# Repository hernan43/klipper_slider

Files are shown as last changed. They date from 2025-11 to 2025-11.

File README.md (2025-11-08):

# DIY Slider Build
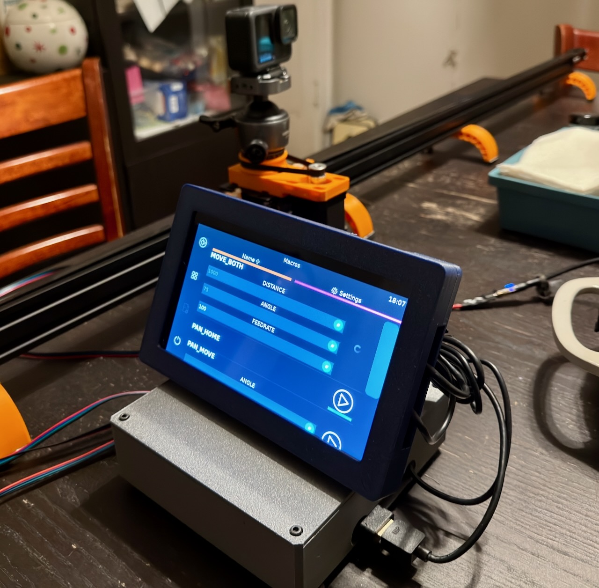
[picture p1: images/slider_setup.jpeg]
Shot of fully built camera slider with pan head and control box/touchscreen


## Hardware
 * [Raspberry Pi 4 Model B 4GB](https://www.pishop.us/product/raspberry-pi-4-model-b-4gb/)
 * [SKR Pico](https://www.amazon.com/BIGTREETECH-Controller-Raspberry-Printing-Motherboard/dp/B09MYKL9MP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)
 * [V slot 2040 aluminum extrusion](https://www.amazon.com/Aluminum-Extrusion-European-Standard-Anodized/dp/B0CLH61BRK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) - whatever length you want
 * [Nema 17 stepper motors](https://www.amazon.com/STEPPERONLINE-Stepper-Bipolar-Printer-Extruder/dp/B0B93J9QZY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)
 * [V slot gantry plate](https://www.amazon.com/SeekLiny-Gantry-Wheels-Aluminum-Extrusion/dp/B0CX7TQQVK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)
 * [6mm idler pulley](https://www.amazon.com/uxcell-Aluminum-Timing-Synchronous-Printer/dp/B0DK3M68YW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)
 * [6mm GT2 timing belt](https://www.amazon.com/Upgrade-Non-Slip-Version-Printer-Printers/dp/B08R93QQ8Z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) - enough for the length of aluminum extrusion you chose
 * [Nema 17 mounting plate](https://www.amazon.com/STEPPERONLINE-Mounting-Bracket-Stepper-Economy/dp/B09LCSBLF8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)
 * [Creality style GT2 belt tensioner](https://www.amazon.com/AEDIKO-Upgraded-Tensioner-Straighten-Creality/dp/B09GF7CN37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)
 * [M4 screws and t-nuts](https://www.amazon.com/Camming-Replacement-Compatible-Standard-Systems/dp/B0B83TGWVT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) - You might need a variety of sizes depending on your part choices

### Pan specific parts
 
 * [35mm thrust bearing](https://www.amazon.com/AXK2035-Thrust-Needle-Bearings-Washers/dp/B0F4X2QCFP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)
 * [8mm thrust bearing](https://www.amazon.com/uxcell-F8-16M-Miniature-Bearings-8x16x5mm/dp/B07QLTXJDH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)
 * [228-2GT-6 Pulley Belt](https://www.amazon.com/dp/B0CMHYBKVN?ref=ppx_yo2ov_dt_b_fed_asin_title&th=1)
 * [3D printed rotating base](https://www.printables.com/model/232492-diy-camera-slider/files)
 * [3D printed mounting plate for tripod head](https://www.printables.com/model/1473628-modified-pan-head-platform)

## Software
 
 * [MainsailOS](https://docs-os.mainsail.xyz/)

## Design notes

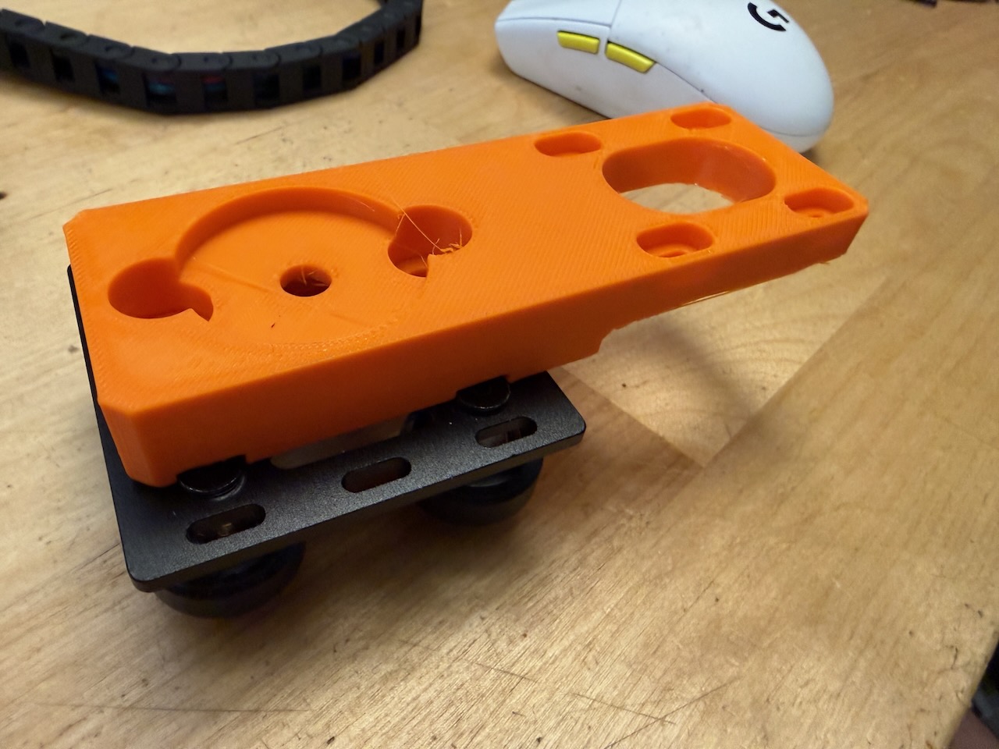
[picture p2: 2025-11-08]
images/slider pan mount.jpeg

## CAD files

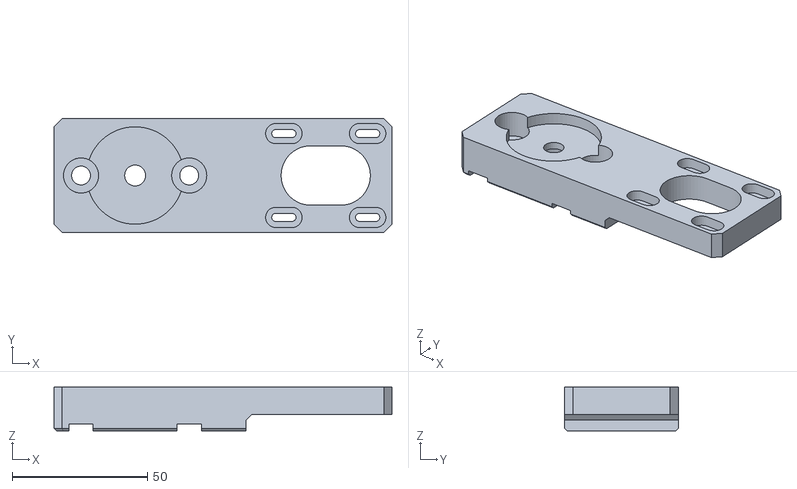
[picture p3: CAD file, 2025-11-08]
STLs/Pan Head mount v14.stl
125.0 x 42.0 x 16.2

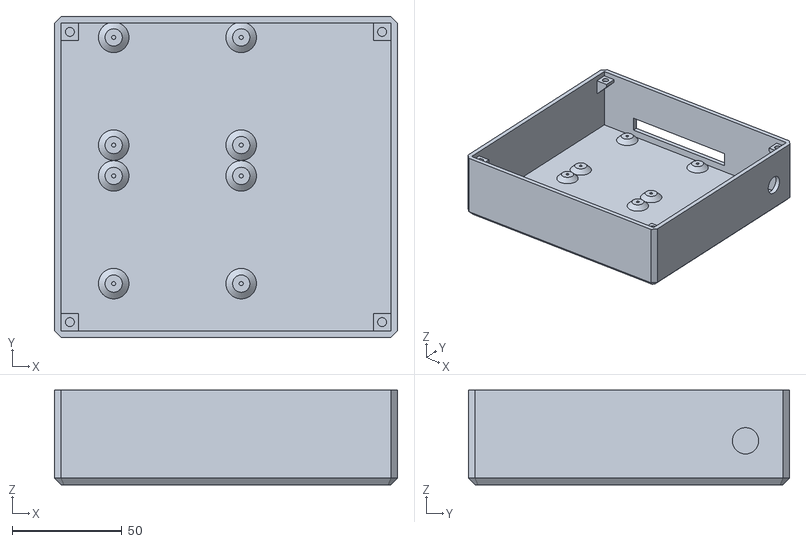
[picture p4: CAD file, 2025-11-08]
STLs/SKR Pico Shell Lower.stl
156.0 x 146.0 x 43.0

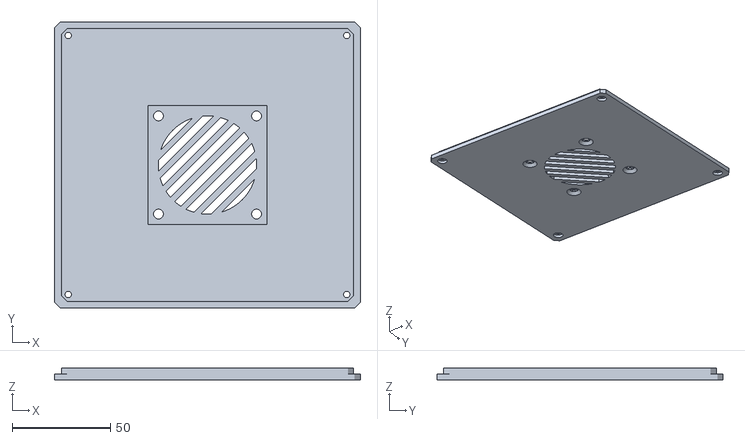
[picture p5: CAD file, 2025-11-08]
STLs/SKR Pico Shell Lid.stl
156.0 x 146.0 x 6.00

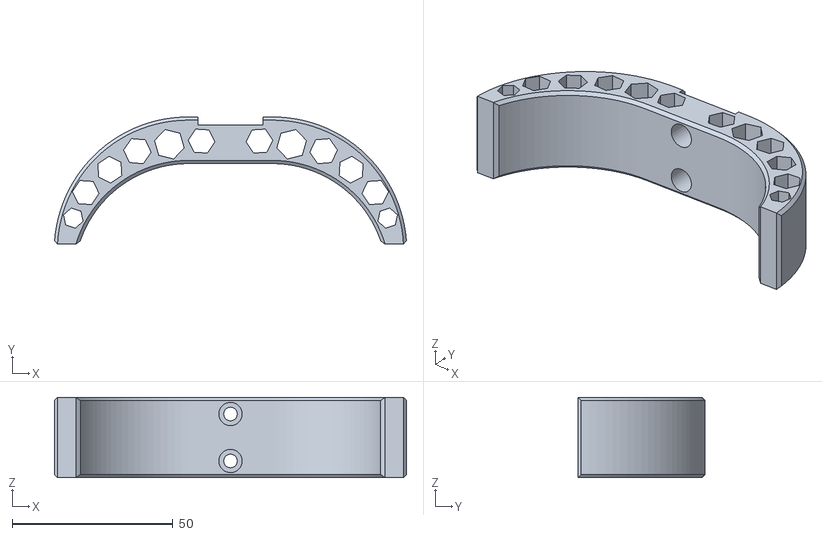
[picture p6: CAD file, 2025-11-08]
STLs/Extrusion foot v10.stl
109.4 x 39.5 x 25.0

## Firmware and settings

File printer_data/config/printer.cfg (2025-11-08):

[include mainsail.cfg]

[mcu]
#serial: /dev/serial/by-id/usb-Klipper_rp2040_504450612065BD1C-if00
serial: /dev/ttyAMA0

# ========= Printer =========
[printer]
kinematics: cartesian
max_velocity: 600
max_accel: 2000
square_corner_velocity: 5.0
# Trick Klipper: disable Z movement (0 height)
max_z_velocity: 1
max_z_accel: 1

# ========= X Axis (Slider) =========
[stepper_x]
step_pin: gpio11
dir_pin: !gpio10
enable_pin: !gpio12
microsteps: 16
rotation_distance: 40.0      # adjust for belt or leadscrew
endstop_pin: tmc2209_stepper_x:virtual_endstop
position_min: 0
position_endstop: 0
position_max: 1100             # slider length in mm
homing_speed: 40
homing_retract_dist: 0
homing_positive_dir: false

[tmc2209 stepper_x]
uart_pin: gpio9
tx_pin: gpio8
uart_address: 0
diag_pin: ^gpio4
run_current: 0.60
stealthchop_threshold: 0
driver_SGTHRS: 50             # higher = more sensitive (try 40–80 range)

# ========= Y Axis (Pan) =========
[stepper_y]
step_pin: gpio6
dir_pin: !gpio5
enable_pin: !gpio7
microsteps: 16
rotation_distance: 40.0     # degrees per motor rev, adjust for gearing
endstop_pin: tmc2209_stepper_y:virtual_endstop
position_endstop: 0
position_min: -180
position_max: 180             # pan range
homing_speed: 20
homing_retract_dist: 0
homing_positive_dir: false

[tmc2209 stepper_y]
uart_pin: gpio9
tx_pin: gpio8
uart_address: 2
diag_pin: ^gpio3
run_current: 0.70
stealthchop_threshold: 0
driver_SGTHRS: 50

# ========= Dummy Z (required placeholder) =========
# This prevents Klipper from complaining that no Z axis exists
[stepper_z]
step_pin: gpio19
dir_pin: gpio28
enable_pin: !gpio2
microsteps: 16
rotation_distance: 8
endstop_pin: ^gpio25
position_endstop: 0.0
position_max: 250

# ========= Macros =========
[idle_timeout]
timeout: 60       # seconds before idle triggers
gcode:
  SET_TMC_CURRENT STEPPER=stepper_x HOLD_CURRENT=0.10
  SET_TMC_CURRENT STEPPER=stepper_y HOLD_CURRENT=0.10

# ========= Sensorless Homing Mode Toggle =========
[gcode_macro SENSORLESS_HOMING_ON]
description: "Enable SpreadCycle for reliable sensorless homing"
gcode:
  M118 Enabling SpreadCycle mode for homing...
  # X axis
  SET_TMC_FIELD STEPPER=stepper_x FIELD=TPWMTHRS VALUE=0
  # Y axis
  SET_TMC_FIELD STEPPER=stepper_y FIELD=TPWMTHRS VALUE=0

[gcode_macro SENSORLESS_HOMING_OFF]
description: "Re-enable quiet StealthChop mode after homing"
gcode:
  M118 Enabling StealthChop for quiet operation...
  # X axis
  SET_TMC_FIELD STEPPER=stepper_x FIELD=TPWMTHRS VALUE=999999
  # Y axis
  SET_TMC_FIELD STEPPER=stepper_y FIELD=TPWMTHRS VALUE=999999

[gcode_macro MOVE_BOTH]
description: "Move slider (X) and pan (Y) together with angle calculation"
gcode:
  {% set x = params.DISTANCE|default(1000)|float %}
  {% set angle = params.ANGLE|default(75)|float %}
  {% set feed = params.FEEDRATE|default(3000)|float %}
  
  {% if angle >= 0 %}
    {% set y = angle * 0.421 %}  # Positive: Y40 = 95°
  {% else %}
    {% set y = angle * 0.4 %}    # Negative: Y36 = 90°
  {% endif %}

  SENSORLESS_HOMING_ON
  G90
  G1 X{x} Y{y} F{feed}
  SENSORLESS_HOMING_OFF

[gcode_macro SLIDE_MOVE]
description: "Move slider to X position (mm)"
gcode:
  SENSORLESS_HOMING_ON
  {% set pos = params.X|float %}
  {% set feed = params.FEEDRATE|default(1500)|float %}
  G90
  G1 X{pos} F{feed}
  G4 P2000    # wait 2 seconds
  M84
  SENSORLESS_HOMING_OFF

[gcode_macro PAN_MOVE]
description: "Rotate pan axis to absolute angle (+ or -)"
gcode:
  {% set angle = params.ANGLE|float %}
  {% set feed = params.F|default(1000)|float %}

  {% if angle >= 0 %}
    {% set distance = angle * 0.421 %}  # Positive: Y40 = 95°
  {% else %}
    {% set distance = angle * 0.4 %}    # Negative: Y36 = 90°
  {% endif %}

  M118 Moving to angle {angle}° (Y={distance}mm)
  G90
  G1 Y{distance} F{feed}

[gcode_macro PAN_HOME]
description: "Return pan axis to zero position"
gcode:
  {% set feed = 1500.0 %}
  G90
  G1 Y0 F{feed}

[gcode_macro SLIDE_HOME]
gcode:
  SENSORLESS_HOMING_ON
  G28 X
  SENSORLESS_HOMING_OFF
  M118 Slider homed

[delayed_gcode PAN_AUTO_HOME]
initial_duration: 2
gcode:
  SET_KINEMATIC_POSITION Y=0

[force_move]
enable_force_move: true

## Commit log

2025-11-08 Batman commit
    [Extrusion foot v10.stl, Pan Head mount v14.stl, SKR Pico Shell Lid.stl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]
2025-11-08 Linked the pan head platform 3D print page
